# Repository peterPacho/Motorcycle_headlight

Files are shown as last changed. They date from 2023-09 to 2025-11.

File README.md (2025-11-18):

## Description
Riding at night is fun but I really didn't like the fact that I couldn't see where I'm going when turning.
This project aims to solve that issue by creating a headlight housing that can rotate, counteracting the motorcycle's lean during the turn, making the projected beam always parallel to the road surface.

Headlight bucket should fit most “Jeep” 7 inch headlights.

[V1 version demo video](https://www.youtube.com/watch?v=rBPONPm-cCk)

There are two MakerFocus TF-Luna lidars attached to the rear of the bike. Distance to the road surface is used to estimate the lean angle. I'm using Lidars since gyro/accelerometers proved to be difficult - I didn't find a way to counteract the centrifugal acceleration during the turn and couldn't obtain reliable data.

The "V3" version changes the overall design of the headlight housing. Migrating from multiple small bearing to two large ones, that would allow the wires to pass through the center, was done to reduce vibrations and friction. Those changes allowed headlight to be more responsive and reliable.

### Noncomprehensive parts list:
-	Arduino (and supporting components like resistors, voltage regulator, capacitors)
-	TMC2209 stepper motor driver
-	NEMA 17 stepper motor
-	16x2 LCD Display
-	80x100x10mm ball bearing x2

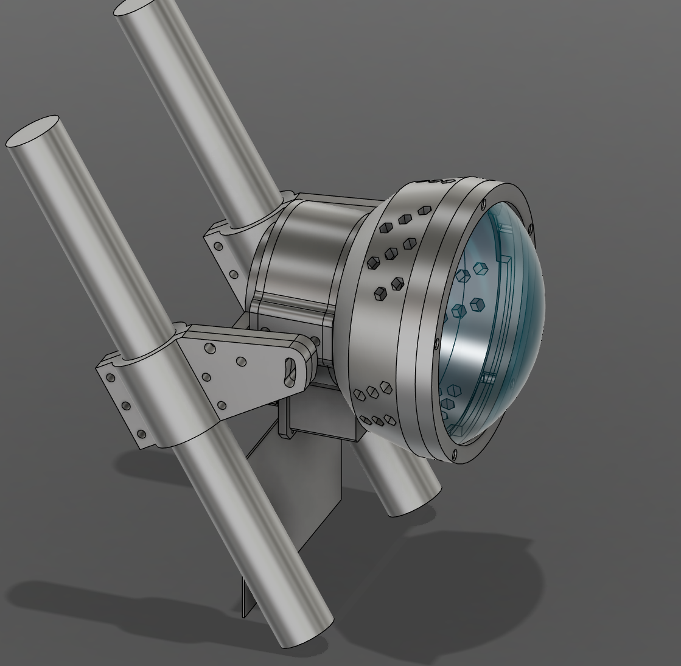
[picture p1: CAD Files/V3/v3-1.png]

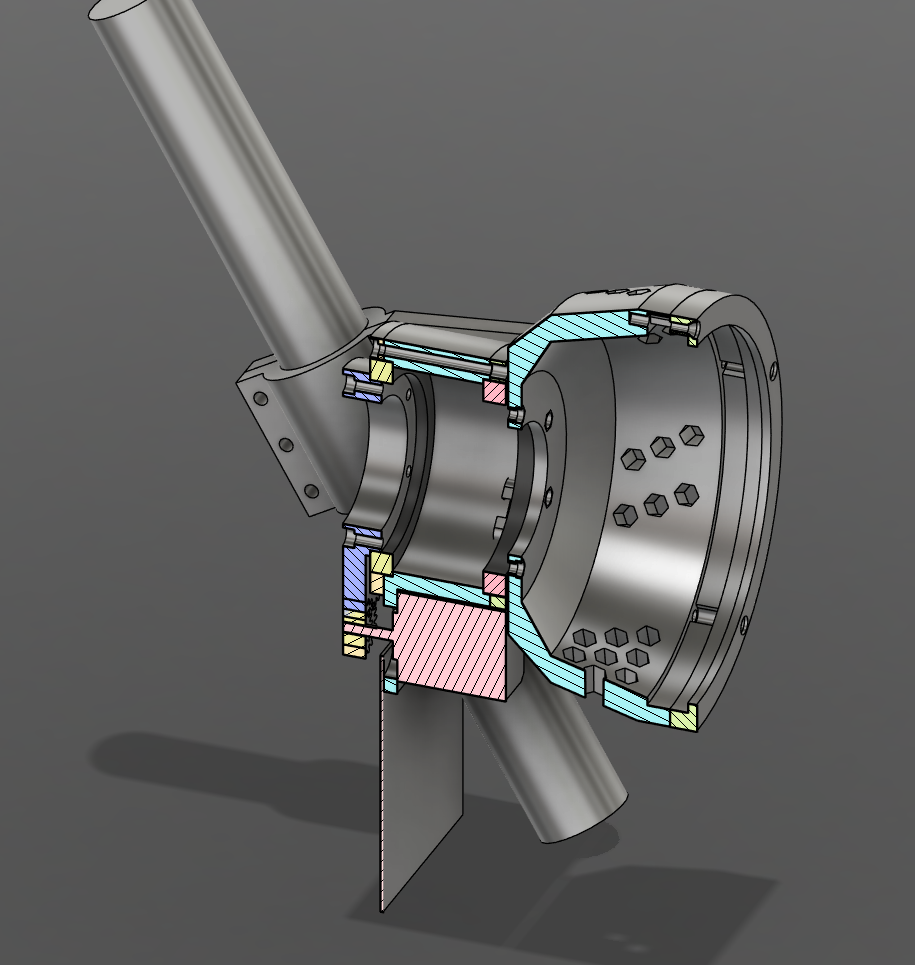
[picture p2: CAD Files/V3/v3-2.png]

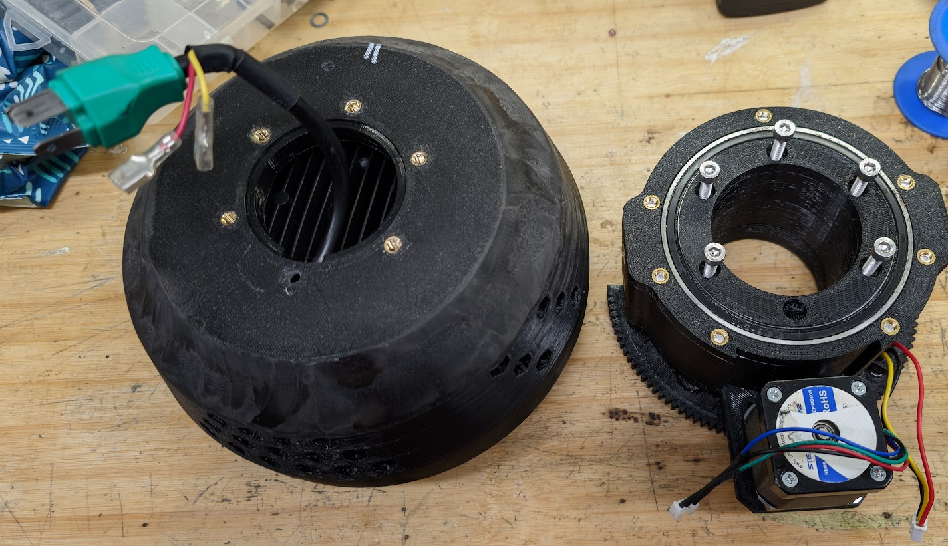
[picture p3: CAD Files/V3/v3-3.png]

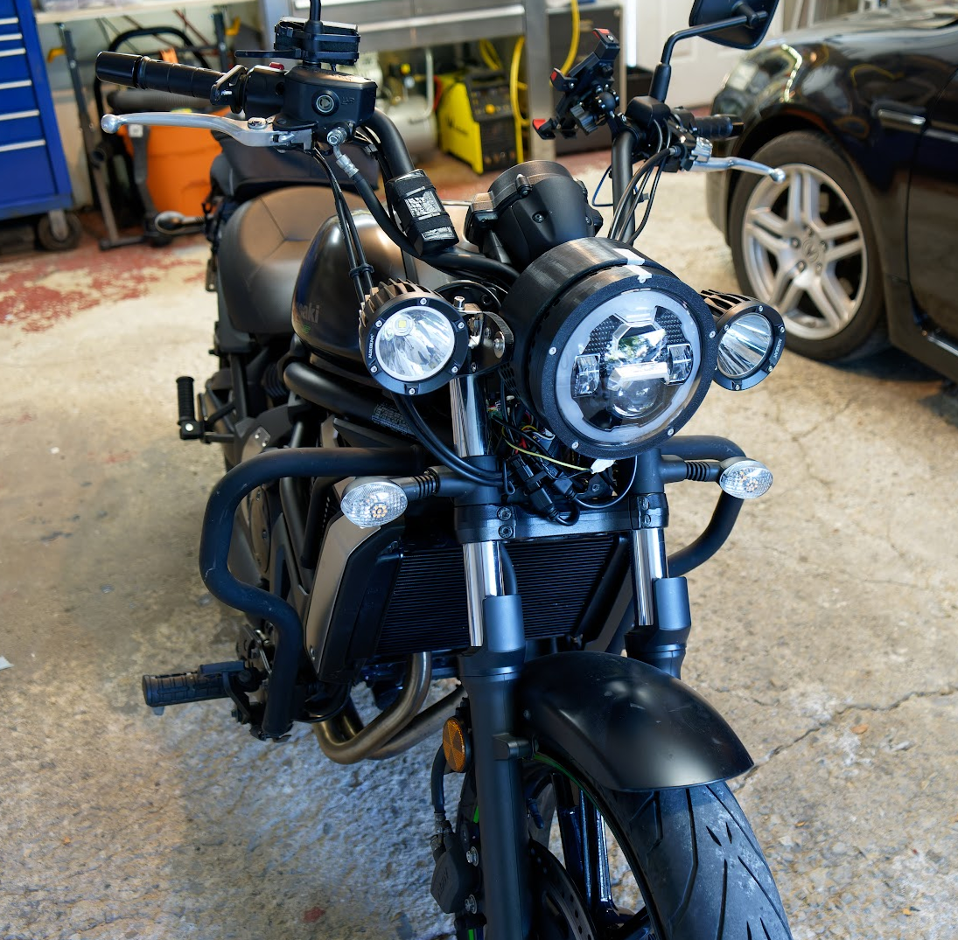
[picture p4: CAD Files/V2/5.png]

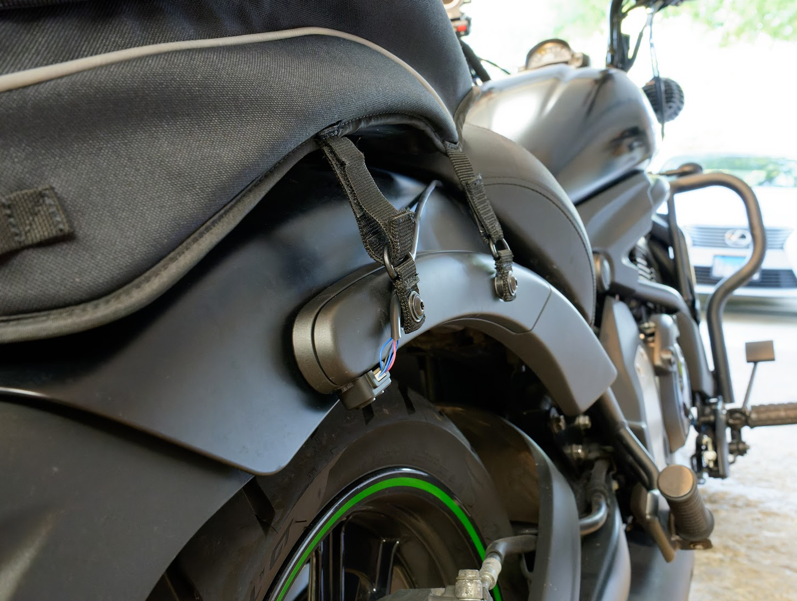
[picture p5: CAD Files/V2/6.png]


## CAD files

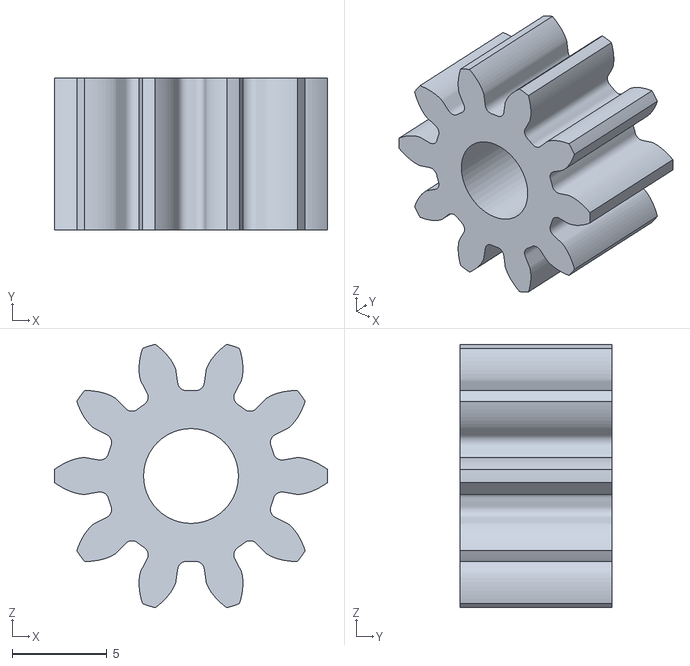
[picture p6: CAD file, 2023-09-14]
CAD Files/STL V2_3/Motorcycle Headlight version 2 v3_Motorcycle Headlight version 2 v3_Headlight outer bucket_1_Spur Gear (10 teeth) - Mod 1.2, Root fill 0.47 (1)_1_Body1.stl
14.4 x 8.00 x 13.9

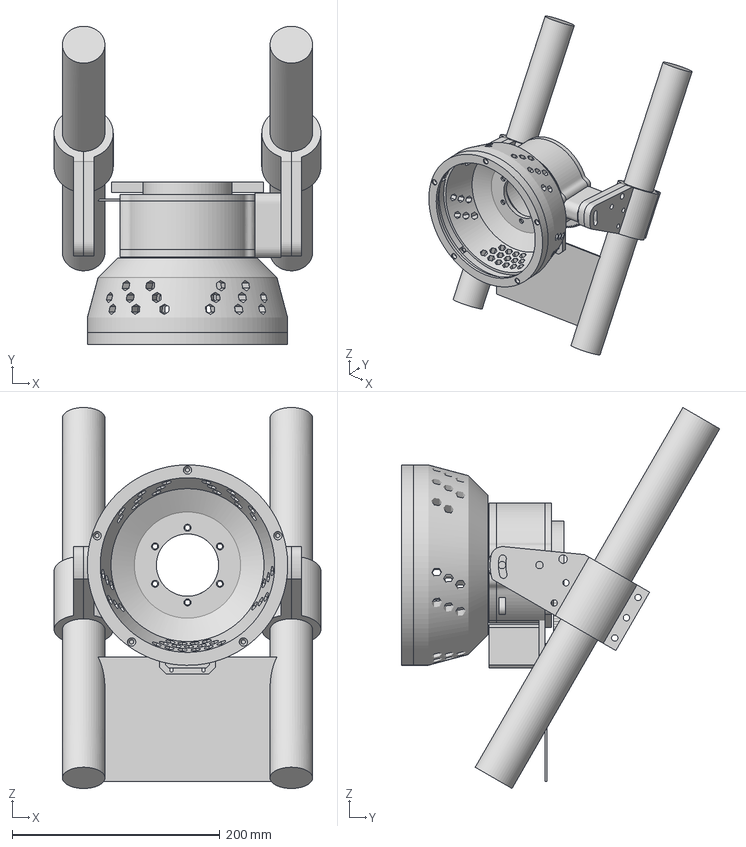
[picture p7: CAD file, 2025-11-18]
CAD Files/V3/Motorcycle Headlight V3-v22.3mf
257.0 x 306.6 x 366.9 mm
A x 2
B x 2
Back
Front-thread-inserts
Mid

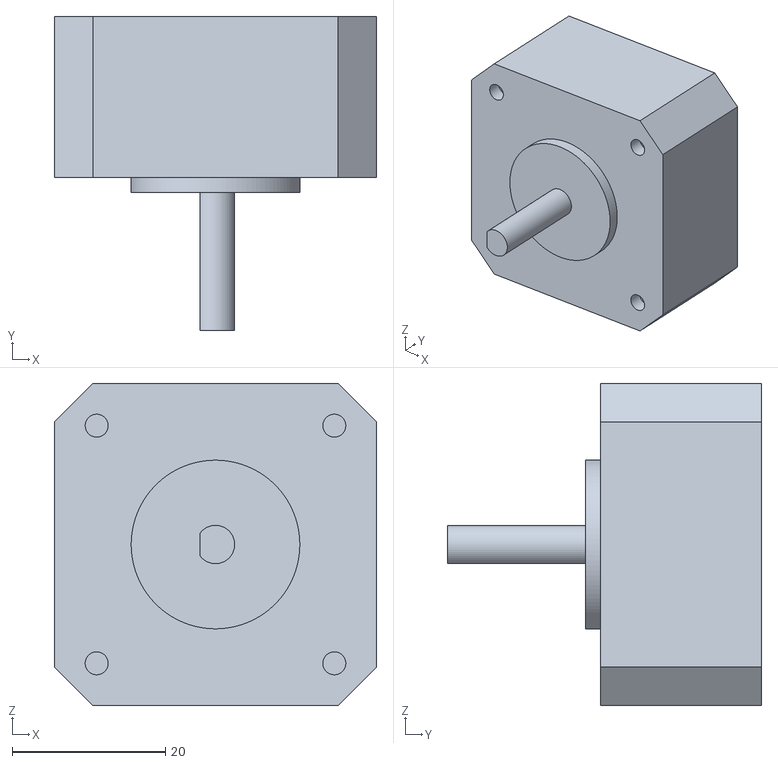
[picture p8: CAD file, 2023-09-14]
CAD Files/STL V2_3/Motorcycle Headlight version 2 v3_Motorcycle Headlight version 2 v3_Headlight outer bucket_1_Stepper_1_Body1.stl
42.0 x 41.0 x 42.0

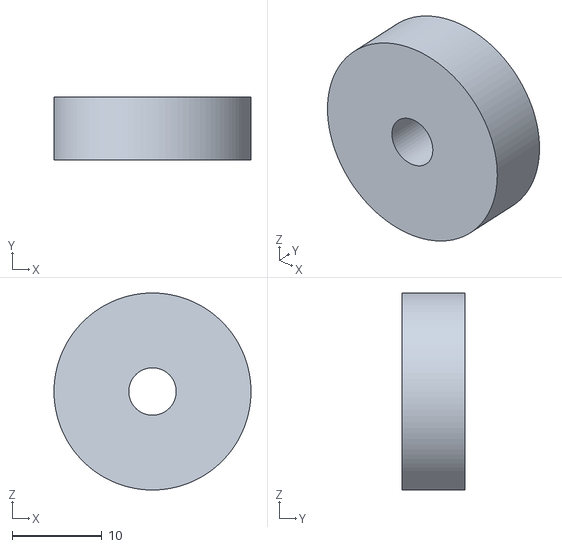
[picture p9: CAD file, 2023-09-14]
CAD Files/STL V2_3/Motorcycle Headlight version 2 v3_Motorcycle Headlight version 2 v3_Headlight inner bucket_1_Bearing_1_Body1.stl
22.0 x 7.00 x 22.0

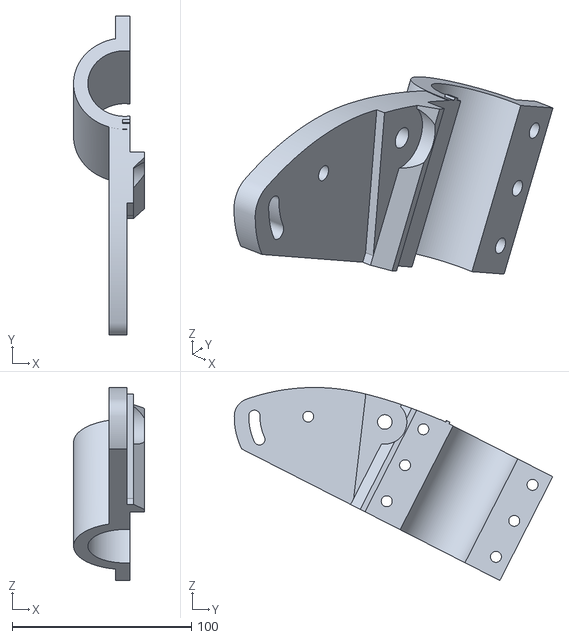
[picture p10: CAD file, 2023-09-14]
CAD Files/STL V2_3/Motorcycle Headlight version 2 v3_Motorcycle Headlight version 2 v3_Forks Mount V2(Mirror) (1)_1_Arm(Mirror) (1)_1_Body1.stl
39.5 x 177.5 x 107.6

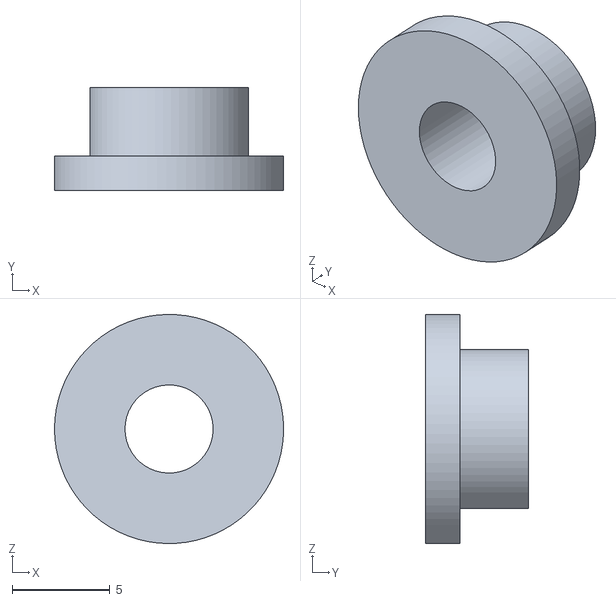
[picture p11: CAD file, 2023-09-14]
CAD Files/STL V2_3/Motorcycle Headlight version 2 v3_Motorcycle Headlight version 2 v3_Headlight inner bucket_1_Bearing sleeve_1_Body1.stl
11.7 x 5.25 x 11.7

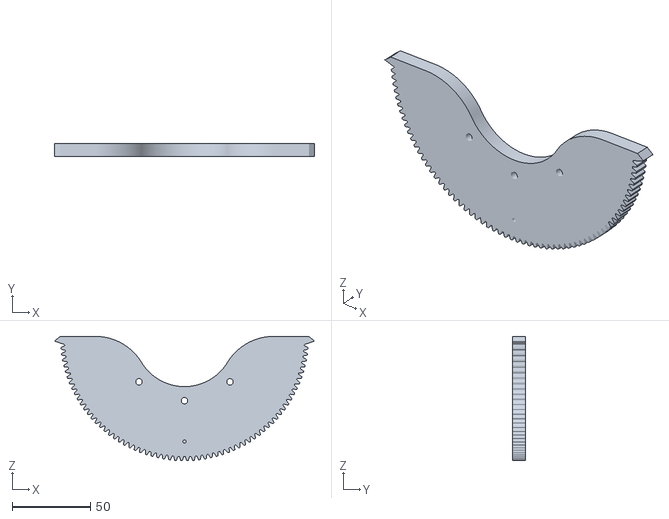
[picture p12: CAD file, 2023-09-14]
CAD Files/STL V2_3/Motorcycle Headlight version 2 v3_Motorcycle Headlight version 2 v3_Headlight inner bucket_1_Spur Gear (130 teeth) Mod 1.2, Root fill 0.47_1_Body1.stl
165.7 x 8.00 x 79.2

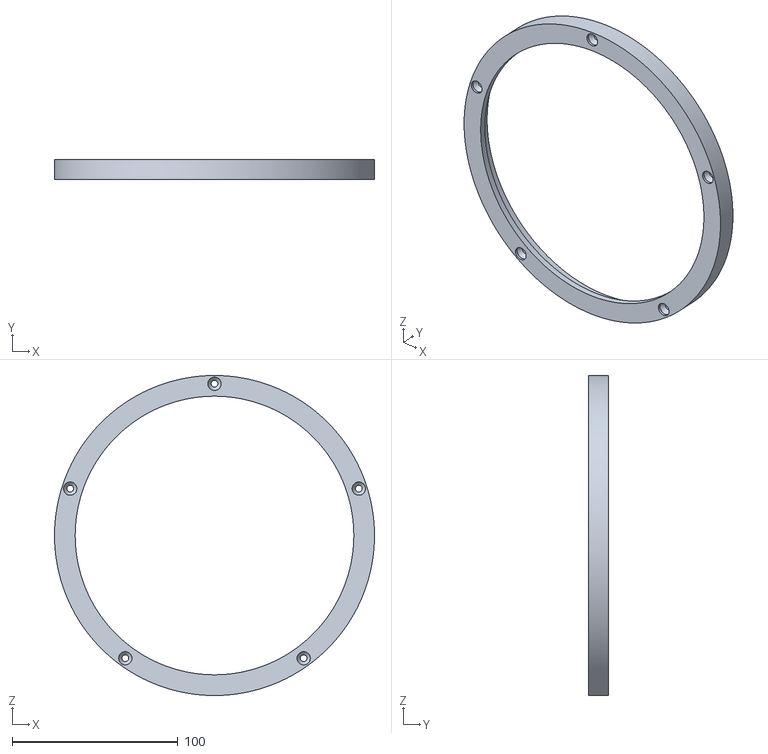
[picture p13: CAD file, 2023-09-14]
CAD Files/STL V2_3/Motorcycle Headlight version 2 v3_Motorcycle Headlight version 2 v3_Headlight inner bucket_1_Front_1_Body1.stl
193.0 x 12.0 x 193.0

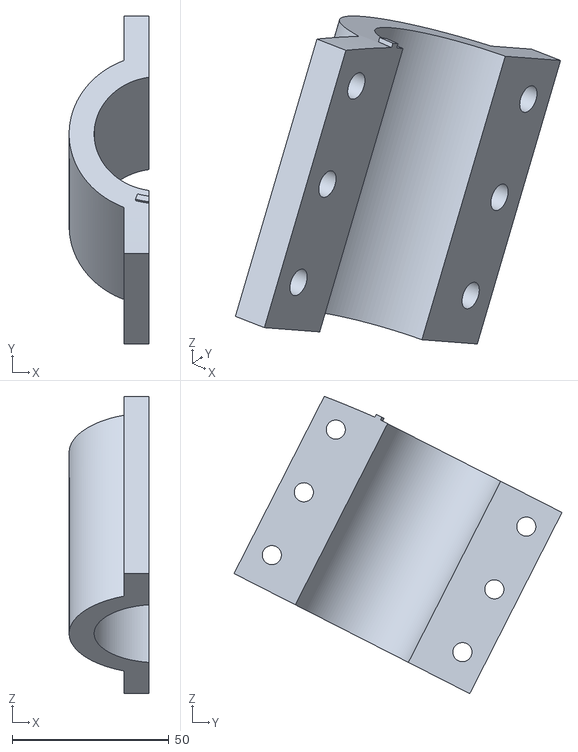
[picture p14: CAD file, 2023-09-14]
CAD Files/STL V2_3/Motorcycle Headlight version 2 v3_Motorcycle Headlight version 2 v3_Forks Mount V2_1_Clamp_1_Clamp.stl
25.5 x 104.8 x 95.0

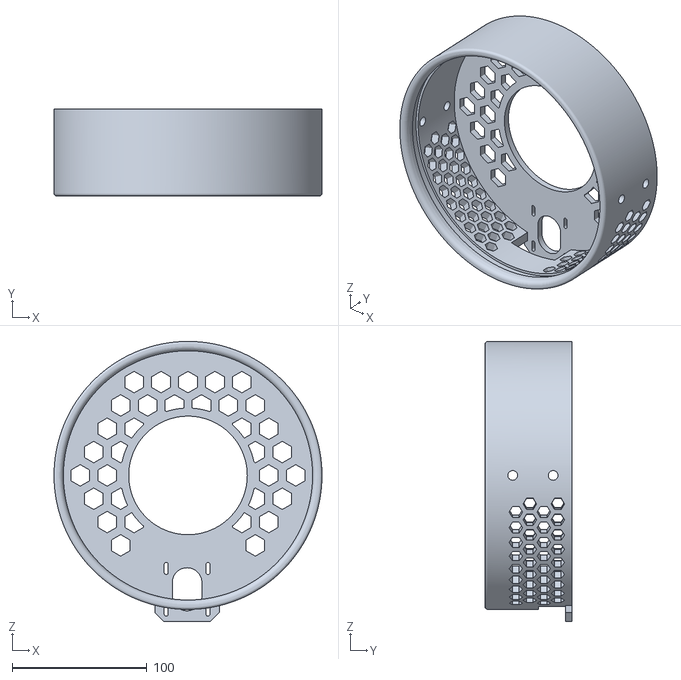
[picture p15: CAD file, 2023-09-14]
CAD Files/STL V2_3/Motorcycle Headlight version 2 v3_Motorcycle Headlight version 2 v3_Headlight outer bucket_1_Outer bucket_1_Body8.stl
199.0 x 64.6 x 208.0

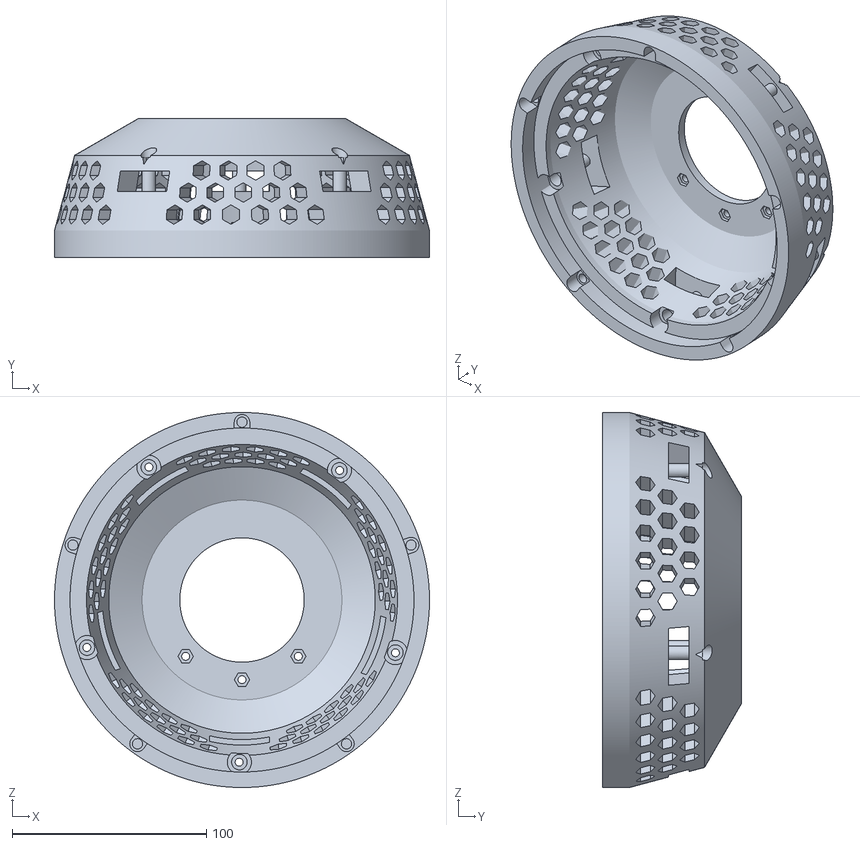
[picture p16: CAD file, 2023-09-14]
CAD Files/STL V2_3/Motorcycle Headlight version 2 v3_Motorcycle Headlight version 2 v3_Headlight inner bucket_1_Inner bucket nuts_1_Body1.stl
193.0 x 71.6 x 193.0

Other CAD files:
CAD Files/STL V2_3/Motorcycle Headlight version 2 v3_Motorcycle Headlight version 2 v3_Forks Mount V2_1_Arm_1_Body4.stl
CAD Files/STL V2_3/Motorcycle Headlight version 2 v3_Motorcycle Headlight version 2 v3_Headlight inner bucket_1_Bearing_1_Body6.stl
CAD Files/STL V2_3/Motorcycle Headlight version 2 v3_Motorcycle Headlight version 2 v3_Headlight inner bucket_1_Bearing_1_Body7.stl
CAD Files/STL V2_3/Motorcycle Headlight version 2 v3_Motorcycle Headlight version 2 v3_Headlight inner bucket_1_Bearing_1_Body9.stl
CAD Files/STL V2_3/Motorcycle Headlight version 2 v3_Motorcycle Headlight version 2 v3_Forks Mount V2(Mirror) (1)_1_Clamp(Mirror) (1)_1_Clamp.stl
CAD Files/STL V2_3/Motorcycle Headlight version 2 v3_Motorcycle Headlight version 2 v3_Headlight inner bucket_1_Bearing_1_Body8.stl
CAD Files/V2/Motorcycle Headlight version 2_v3.f3d

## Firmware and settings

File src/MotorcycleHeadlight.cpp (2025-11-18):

#include <Arduino.h>
#include <Wire.h>
#include <TMCStepper.h>	  // https://github.com/teemuatlut/TMCStepper
#include <AccelStepper.h> // https://github.com/teemuatlut/TMCStepper/blob/master/examples/TMC_AccelStepper/TMC_AccelStepper.ino
#include <LiquidCrystal_I2C.h>
#include <avr/eeprom.h>
#include <TFLI2C.h> // https://github.com/budryerson/TFLuna-I2C

// comment out to disable log/debug/serial commands and reduce sketch size
// #define DEBUG_ON

/*
	Comment out if uploading the sketch for the first time so
	it writes default settings to the Arduino's eeprom
*/
// #define RESTORE_DEFAULT_SETTINGS

/*
	Arduino pin-out. SDA (white wire) - A4, SCL (yellow/green wire) - A5
*/
const uint8_t
	DRIVER_ENABLE = 9,
	DRIVER_DIRECTION = 10,
	DRIVER_STEP = 13,
	DRIVER_SWCLCK = 11,
	DRIVER_TX = 6,
	DRIVER_RX = 12,

	HALL_SENSOR = 4, // sensor that detects the center position of the headlight
	BUTTON1 = 7,
	BUTTON2 = 8,
	BUTTON3 = A1,
	BUTTON4 = A2,
	LCD_BRIGHTNESS = 3,	   // must be a PWM pin, used to set custom LCD brightness that extends the build-in on/off
	VOLTAGE_SENSE = A0,	   // connected to voltage divider and 12V input
	LUNA_ENABLE_RELAY = 2; // pin that disables one of Luna modules so the address of the other one can be changed

#define DRIVER_ADDRESS 0b00
#define DRIVER_RSENSE 0.11f
#define MPU 0x68
#define LUNA_ADDRESS_1 0x10 // this must be the default luna address
#define LUNA_ADDRESS_2 0x11 // luna that is not connected through relay will have address changed to this value

/*
	With 72:8 gear ratio (9:1),
	stepper motor having 1.8 degrees per step
	and microsteps set to 16
	it takes 360 * 9 * 16 / 1.8 = 28800 steps for full rev.

	With 130:10 / 13:1 gear ratio and 2 micro steps = 5200
	With 120:12 and 2 micro steps = 4800
	With 120:20 and 2 micro steps = 2400
*/
#define DRIVER_MICROSTEPS 2					  // to disable microsteps change this to 0
#define STEPS_PER_REVOLUTION 2400			  // used by the centering function
#define STEPS_LIMIT STEPS_PER_REVOLUTION * .2 // How many steps it takes to reach end of travel from the center. Limits the headlight's maximum angle.

SoftwareSerial SoftSerial(DRIVER_RX, DRIVER_TX);
TMC2209Stepper TMCdriver(&SoftSerial, DRIVER_RSENSE, DRIVER_ADDRESS);
AccelStepper stepper = AccelStepper(stepper.DRIVER, DRIVER_STEP, DRIVER_DIRECTION);
LiquidCrystal_I2C lcd(0x27, 16, 2);
TFLI2C tflI2C;

/*
	The idea to store/save settings like this it taken from
	catalkn's post at https://forum.arduino.cc/t/how-to-save-configuration/45314/6
*/
struct SETTINGS_S
{
	int DRIVER_MAX_SPEED = STEPS_PER_REVOLUTION / 4; // in steps per second, with 2A and 120:20 gear ratio, this should be ~500
	int DRIVER_MAX_ACC = STEPS_PER_REVOLUTION / 4;	 // in steps per second, with 2A and 120:20 gear ratio, this should be ~1500
	int DRIVER_CURRENT = 1000;						 // in mA?, bigger nema should be fine at 2A
	int DISPLAY_BRIGHTNESS = 100;					 // 0-255
	int SENSOR_UPDATE_TIME = 25;					 // in ms, how often to read data from the lunas
	int STEPS_LIMIT_ALLOWED = STEPS_LIMIT;			 // STEPS_LIMIT sets how many steps are allowed by hardware (physical stop), this limits it further
	int MOVE_THRESHOLD = 2;							 // how many steps off "correct" position before is starts moving
	int MOVE_THRESHOLD_CENTER = 5;					 // how many steps off center before it starts moving
	int SPEED_THRESHOLD = 200;						 // if current speed above this # of steps, don't read lunas to prevent skipping the steps
	char STARTUP_MODE = -1;							 // what should be the mode after first start, -1 default, 0 or 1 will call calibration function
	float VOLTAGE_WEIGHTING_PARAMETER = 0.1;		 // to filter voltage readings
	float SENSOR_WEIGHTING_PARAMETER = 0.1;			 // to filter LUNA readings
} const DEFAULT_SETTINGS;

SETTINGS_S SETTINGS = DEFAULT_SETTINGS;
// void eeprom_update_block(const void*, void*, size_t); //defined so VS code doesn't complain
// void eeprom_read_block(void*, const void*, size_t);

void loadSettings()
{
	eeprom_read_block((void *)&SETTINGS, (void *)0, sizeof(SETTINGS));

	TMCdriver.rms_current(SETTINGS.DRIVER_CURRENT);
	stepper.setMaxSpeed(SETTINGS.DRIVER_MAX_SPEED);
	stepper.setAcceleration(SETTINGS.DRIVER_MAX_ACC);
	analogWrite(LCD_BRIGHTNESS, SETTINGS.DISPLAY_BRIGHTNESS);
}

void saveSettings()
{
	eeprom_update_block((const void *)&SETTINGS, (void *)0, sizeof(SETTINGS));
}

/*
	If uploading the sketch first time call this function!
	Don't enable the stepper driver or bad things might happen.
*/
void restoreDefaultSettings()
{
	SETTINGS = DEFAULT_SETTINGS;
	TMCdriver.rms_current(SETTINGS.DRIVER_CURRENT);
	stepper.setMaxSpeed(SETTINGS.DRIVER_MAX_SPEED);
	stepper.setAcceleration(SETTINGS.DRIVER_MAX_ACC);
	analogWrite(LCD_BRIGHTNESS, SETTINGS.DISPLAY_BRIGHTNESS);

	saveSettings();
}

char mode = -1; // used in main loop to turn on/off gyro function

// debouncing class for simple buttons, default for them is high (internal pull up)
unsigned long lastButtonEvent = 0; // keeps time when was the button pressed last time
class button
{
public:
	// constructor that sets all variables to default
	button(byte buttonID_c)
	{
		pinMode(buttonID_c, INPUT_PULLUP);

		// update all variables
		buttonID = buttonID_c;
		buttonDebounce = 0;
		buttonLastState = HIGH;
		buttonCurrentState = HIGH;
		buttonPressUsed = true;
	}

	// returns 1 if pressed, returns 2 if being hold
	int state()
	{
		// read actual button state
		buttonCurrentState = digitalRead(buttonID);

		// check if it changed from last time, if it did take note of the time
		if (buttonCurrentState != buttonLastState)
			buttonDebounce = millis();

		// update the last state variable
		buttonLastState = buttonCurrentState;

		// check if button is being held down
		if (millis() - buttonDebounce > buttonHoldTimer && buttonCurrentState == LOW)
		{
			lastButtonEvent = millis();

			// prevent from setting the "isPressed" and "isHeld" signal simultaneously
			buttonPressUsed = true;

			return 2;
		}

		// now check if button is in its current state for long enough, but trigger only if button is let go
		else if ((millis() - buttonDebounce) > buttonDebounceDelay && millis() - buttonDebounce < buttonHoldTimer)
		{
			// remember to return true only once per button press
			// to prevent value increase when button is being hold
			if (!buttonPressUsed && buttonCurrentState == HIGH)
			{
				buttonPressUsed = true;

				// if so, update the optional variable, if set
				lastButtonEvent = millis();

				return 1;
			}

			// if not pressed, reset the 'use' variable
			if (buttonCurrentState == LOW)
				buttonPressUsed = false;
		}

		return 0;
	}

private:
	byte buttonID;								  // holds button id, like A1
	unsigned long buttonDebounce;				  // holds time when button changed last time
	int buttonLastState;						  // what was last button state
	int buttonCurrentState;						  // what is current state
	bool buttonPressUsed;						  // if button was determined to be pressed, use this to return true only once
	const unsigned long buttonDebounceDelay = 20; // minimum delay between change of signals
	const unsigned long buttonHoldTimer = 400;	  // how long to hold the button before it's considered being hold
};
button buttonOK(BUTTON4);
button buttonUp(BUTTON3);
button buttonDown(BUTTON1);
button buttonESC(BUTTON2);

/*
	Finds the center / calibrates the stepper using the hall sensor.
*/
void calibratePosition()
{
	// setup
	int direction = 1;

	lcd.clear();
	lcd.setCursor(0, 0);
	lcd.print(F("Calibrating"));
	lcd.setCursor(4, 1);
	lcd.print(F("position..."));
	if (digitalRead(DRIVER_ENABLE))
	{
		stepper.enableOutputs();
		delay(300);
	}
	stepper.setMaxSpeed(SETTINGS.DRIVER_MAX_SPEED / 3);
	stepper.setAcceleration(SETTINGS.DRIVER_MAX_ACC / 3);

	// if already calibrated before, move to 0 to reduce time
	// if just started or already on 0 this function returns 0
	if (stepper.currentPosition())
	{
		stepper.moveTo(0);
		while (stepper.distanceToGo())
			stepper.run();
		// if moved to 0 but still didn't reach HALL (due to some missed steps??) go a bit further
		if (digitalRead(HALL_SENSOR))
			stepper.moveTo(STEPS_PER_REVOLUTION * 0.04);
		while (stepper.distanceToGo())
			stepper.run();
	}

	// arbitrary multiplier - want to move not more than less than 45 degrees
	stepper.move(-STEPS_PER_REVOLUTION * 0.25);

	while (stepper.distanceToGo() != 0 && digitalRead(HALL_SENSOR))
	{
		stepper.run();
	}

	stepper.setCurrentPosition(0);

	//	if hall still reads high, we must be past it (and stalled on the end stop), so rotate back to the middle
	if (digitalRead(HALL_SENSOR))
	{
		direction = direction * -1; // set so next steps of finding the center accelerate in the same direction

		stepper.move(STEPS_PER_REVOLUTION * 0.3);

		while (stepper.distanceToGo() != 0 && digitalRead(HALL_SENSOR))
		{
			stepper.run();
		}
	}

	stepper.setCurrentPosition(0);

	// at this point we more or less should be in the middle
	// hall should read 0
	// so do small steps to actually find the middle
	stepper.setMaxSpeed(SETTINGS.DRIVER_MAX_SPEED / 6);
	stepper.setAcceleration(SETTINGS.DRIVER_MAX_ACC / 6);

	// again arbitrary multiplier - too small and we don't reach other side of the magnet
	stepper.move(-STEPS_PER_REVOLUTION * 0.04 * direction);

	while (stepper.distanceToGo() != 0 && !digitalRead(HALL_SENSOR))
	{
		stepper.run();
	}

	// reached some point where hall no longer reads 0
	// reset position to 0
	// move in other direction until hall reads 0 and then reads 1 again

	stepper.setCurrentPosition(0);
	stepper.move(STEPS_PER_REVOLUTION * 0.04 * direction);

	while (stepper.distanceToGo() != 0 && digitalRead(HALL_SENSOR))
	{
		stepper.run();
	}
	while (stepper.distanceToGo() != 0 && !digitalRead(HALL_SENSOR))
	{
		stepper.run();
	}

	// go back to the previous settings
	stepper.setMaxSpeed(SETTINGS.DRIVER_MAX_SPEED);
	stepper.setAcceleration(SETTINGS.DRIVER_MAX_ACC);

	// now reached other side of the hall range, so actual middle position is somewhere in between
	stepper.moveTo(stepper.currentPosition() / 2);

	while (stepper.distanceToGo() != 0)
		stepper.run();

	// now we are in the actual middle position
	stepper.setCurrentPosition(0);

	lcd.clear();
}

#ifdef DEBUG_ON
/*
	Taken from https://learn.adafruit.com/scanning-i2c-addresses/arduino
*/
void findDevices()
{
	byte error, address;
	int nDevices;

	Serial.println(F("Scanning..."));

	nDevices = 0;
	for (address = 1; address < 127; address++)
	{
		// The i2c_scanner uses the return value of
		// the Write.endTransmission to see if
		// a device did acknowledge to the address.
		Wire.beginTransmission(address);
		error = Wire.endTransmission();

		if (error == 0)
		{
			Serial.print(F("I2C device found at address 0x"));
			if (address < 16)
				Serial.print(F("0"));
			Serial.println(address, HEX);

			nDevices++;
		}
		else if (error == 4)
		{
			Serial.print(F("Unknown error at address 0x"));
			if (address < 16)
				Serial.print(F("0"));
			Serial.println(address, HEX);
		}
	}
	if (nDevices == 0)
		Serial.println(F("No I2C devices found\n"));
	else
		Serial.println(F("done\n"));
}

/*
	Processes the serial commands for debugging
*/
void serialCommands()
{
	if (Serial.available())
	{
		String data = Serial.readString();

		switch (data.charAt(0))
		{
		case 's':
		{
			int speed = data.substring(1).toInt();

			if (speed == 0)
			{
				stepper.disableOutputs();
				Serial.println(F("Stepper disabled"));
			}
			else
			{
				Serial.print(F("Speed set to "));
				Serial.println(speed);
				stepper.enableOutputs();
				stepper.setMaxSpeed(speed);
			}
			break;
		}

		case 'p':
		{
			int position = data.substring(1).toInt();
			Serial.print(F("Moving stepper to position "));
			Serial.println(position);
			stepper.moveTo(position);
			break;
		}

		case 'a':
		{
			int speed = data.substring(1).toInt();

			Serial.print(F("Acceleration set to "));
			Serial.println(speed);
			stepper.enableOutputs();
			stepper.setAcceleration(speed);
			break;
		}

		case 'c':
		{
			calibratePosition();
			break;
		}
		case 'd':
		{
			Serial.println(F("Stepper disabled."));
			stepper.disableOutputs();
			break;
		}
		default:
			Serial.println(F("Unknown command!"));
		}
	}
}

#endif

/*
	Those values were obtained by gathering data on different voltage levels and doing
	the linear curve fit in LoggerPro. More accurate than calculating from resistor's values used and requires less brain power.
*/
float voltMeter()
{
	// static byte voltageHistoryCounter = 0;
	// static int voltageHistory[VOLTAGE_HISTORY_SIZE] = {0};

	// voltageHistory[voltageHistoryCounter] = analogRead(VOLTAGE_SENSE);
	// voltageHistoryCounter++;
	// if (voltageHistoryCounter >= VOLTAGE_HISTORY_SIZE)
	// 	voltageHistoryCounter = 0;

	// unsigned long historySum = 0;
	// for (int i = 0; i < VOLTAGE_HISTORY_SIZE; i++)
	// {
	// 	historySum += voltageHistory[i];
	// }
	static float previousValue = 0;
	float currentValue = (float)analogRead(VOLTAGE_SENSE) * 0.02764 + 0.0708;
	previousValue = previousValue * (1 - SETTINGS.VOLTAGE_WEIGHTING_PARAMETER) + currentValue * SETTINGS.VOLTAGE_WEIGHTING_PARAMETER;

	return currentValue;
}

void setup()
{
#ifdef RESTORE_DEFAULT_SETTINGS
	restoreDefaultSettings();
#endif

	eeprom_read_block((void *)&SETTINGS, (void *)0, sizeof(SETTINGS));

#ifdef DEBUG_ON
	Serial.begin(115200);
	Serial.print(F("Setup begin...  "));
#endif
	SoftSerial.begin(9600);
	TMCdriver.beginSerial(9600);

	Wire.begin();

	lcd.init();
	lcd.noBacklight(); // as brightness is controlled by arduino, LCD is modified to allow that
	analogWrite(LCD_BRIGHTNESS, SETTINGS.DISPLAY_BRIGHTNESS);
	lcd.clear();
	lcd.setCursor(0, 0);
	lcd.print(F("Starting..."));

	digitalWrite(DRIVER_ENABLE, HIGH);
	pinMode(DRIVER_ENABLE, OUTPUT);
	pinMode(DRIVER_DIRECTION, OUTPUT);
	pinMode(DRIVER_STEP, OUTPUT);
	pinMode(HALL_SENSOR, INPUT_PULLUP);
	pinMode(VOLTAGE_SENSE, INPUT);

	/*
		disable one of the luna sensors to change other luna's address
		luna power connected to normally closed relay, so writing 1 opens the relay
	*/
	pinMode(LUNA_ENABLE_RELAY, OUTPUT);
	digitalWrite(LUNA_ENABLE_RELAY, 1);

	TMCdriver.begin();
	TMCdriver.rms_current(SETTINGS.DRIVER_CURRENT);
	TMCdriver.pwm_autoscale(1);
	TMCdriver.microsteps(DRIVER_MICROSTEPS);

	stepper.setMaxSpeed(SETTINGS.DRIVER_MAX_SPEED);
	stepper.setAcceleration(SETTINGS.DRIVER_MAX_ACC);
	stepper.setEnablePin(DRIVER_ENABLE);
	stepper.setPinsInverted(false, false, true);
	stepper.disableOutputs();

	if (SETTINGS.STARTUP_MODE != -1)
	{
		calibratePosition();
		mode = SETTINGS.STARTUP_MODE;
	}

	// if luna found on the default address, change it
	// if arduino rebooted without power cycling luna, it won't respond to this address
	Wire.beginTransmission(LUNA_ADDRESS_1);
	if (Wire.endTransmission() == 0)
	{
		tflI2C.Set_I2C_Addr(LUNA_ADDRESS_2, LUNA_ADDRESS_1);
	}
	digitalWrite(LUNA_ENABLE_RELAY, 0); // enable the second luna

#ifdef DEBUG_ON
	Serial.println(F(" done."));
#endif
}

/*
	Used to set numerical setting values.

	Input:
		- startValue - current setting/value
		- min, max - allowed range for that setting
		- multiplier - how much value should change per single button event

	Returns:
		- if ESC button pressed - original/unchanged startValue
		- if OK pressed - currently set/displayed value
*/
int menuInner(int startValue, int min, int max, int y, int multiplier = 1)
{
	int setValue = startValue;
	int displayedValue = startValue + 1; // to make sure display updates this time

	// figure out maximum number of characters needed to display the value
	int maxLength = String(max).length();
	int maxLength2 = String(min).length() + 1;
	if (maxLength2 > maxLength)
		maxLength = maxLength2;

	while (1)
	{
		if (displayedValue != setValue)
		{
			// clear the fields
			for (int i = 16 - maxLength; i <= 15; i++)
			{
				lcd.setCursor(i, y);
				lcd.print(F(" "));
			}

			// figure out how many characters we need
			lcd.setCursor(16 - String(setValue).length(), y);

			lcd.print(setValue);

			displayedValue = setValue;
		}

		if (buttonUp.state())
		{
			setValue += multiplier;
			if (setValue > max)
				setValue = max;
		}
		else if (buttonDown.state())
		{
			setValue -= multiplier;
			if (setValue < min)
				setValue = min;
		}
		else if (buttonESC.state())
		{
			return startValue;
		}
		else if (buttonOK.state() == 1)
		{
			return setValue;
		}
	}
}
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
void loop()
{
#ifdef DEBUG_ON
	serialCommands();
	static unsigned long lastLogEvent = 0;
	if (millis() - lastLogEvent > 500)
	{
		Serial.println(stepper.speed());

		lastLogEvent = millis();
	}

#endif

	static float bikeLeanAngle = 0;
	static int previousTarget = 0; // what was the target stepper position
	int16_t lunaDist1 = 0, lunaDist2 = 0;
	bool lunaReadingResult = false;

	/*

	*/
	do
	{
		stepper.run();
	} while (abs(stepper.speed()) > SETTINGS.SPEED_THRESHOLD);
	/*
		Todo:
		- this "300" value, make it a setting
		- migrate settings menu from 5160 branch
	*/

	/*
		Update the sensors.
		Reading one sensor at the time.
	*/
	static unsigned long lastSensorUpdate = 0;
	bool updateLunas = millis() - lastSensorUpdate > (unsigned long)SETTINGS.SENSOR_UPDATE_TIME;
	if (updateLunas)
	{
		lunaReadingResult = tflI2C.getData(lunaDist1, LUNA_ADDRESS_1);
	}

	stepper.run();

	/*
		Reading second luna
	*/
	// unsigned long start = micros(), end;
	if (updateLunas)
	{
		lunaReadingResult = lunaReadingResult && tflI2C.getData(lunaDist2, LUNA_ADDRESS_2);

		if (lunaReadingResult)
		{
			bikeLeanAngle = getBikeAngle(lunaDist1 - lunaDist2);

			lastSensorUpdate = millis();
		}
	}

	/*
		Stepper motor control.
	*/
	if (mode == 1)
	{
		// bikeLeanAngle is in degrees off center
		int newTarget = bikeLeanAngle * STEPS_PER_REVOLUTION / 4 / 90;

		if (abs(newTarget) < SETTINGS.MOVE_THRESHOLD_CENTER)
		{
			newTarget = 0;
			previousTarget = 0;
			stepper.moveTo(0);
		}
		else if (abs(newTarget - previousTarget) > SETTINGS.MOVE_THRESHOLD)
		{
			if (newTarget > SETTINGS.STEPS_LIMIT_ALLOWED)
				newTarget = SETTINGS.STEPS_LIMIT_ALLOWED;
			else if (newTarget < -SETTINGS.STEPS_LIMIT_ALLOWED)
				newTarget = -SETTINGS.STEPS_LIMIT_ALLOWED;

			stepper.moveTo(newTarget);

			previousTarget = newTarget;
		}
	}
	// end = micros();
	// end = end - start;
	// if (end > 100)
	// 	Serial.println(end);

	// if stepper not in target position don't run rest of the function.
	// less important parts after this step
	if (stepper.distanceToGo())
	{
		return;
	}

	/*
		Check for user input.
		Only very important button checks here as it's possibly
		done when stepper driver is running.
	*/
	switch (buttonOK.state())
	{
	case 1:
		if (mode == -1)
		{
			calibratePosition();
			mode = 0;
		}
		else
		{
			if (mode == 0)
				mode = 1;
			else
				mode = 0;

			if (!mode)
			{
				stepper.moveTo(0);
				previousTarget = 0;
			}
		}
		break;

		// if button is held down, recalibrate without changing the mode
	case 2:
		int modeSave = mode;

		calibratePosition();

		if (modeSave == 1)
			mode = 1;
		else
			mode = 0;

		break;
	}

	if (buttonESC.state())
	{
		// if we were calibrated and possibly running, go back to the center before entering the menu
		if (mode != -1)
			stepper.moveTo(0);
		while (stepper.distanceToGo())
			stepper.run();

		stepper.disableOutputs();
		mode = -1;
		menu_main();
		return;
	}
	else if (buttonDown.state() == 2)
	{
		mode = -1;
		stepper.disableOutputs();
	}

	/*
		Update the display.
	*/
	static unsigned long lastDisplayUpdate = 0;
	if (millis() - lastDisplayUpdate > 300)
	{
		lcd.clear();
		lcd.setCursor(0, 0);

		lcd.print(F("Status:"));
		lcd.setCursor(0, 1);
		if (mode == 0)
			lcd.print(F("OFF"));
		else if (mode == 1)
			lcd.print(F("ON"));
		else if (mode == -1)
		{
			static byte msg_counter = 0;

			if (msg_counter < 3)
				lcd.print(F("press OK"));
			else if (msg_counter < 6)
				lcd.print(F("to"));
			else
				lcd.print(F("calibrate"));

			msg_counter++;
			if (msg_counter > 9)
				msg_counter = 0;
		}
		else
			lcd.print(F("err"));

		float volts = voltMeter();
		if (volts >= 10)
			lcd.setCursor(10, 1);
		else
			lcd.setCursor(11, 1);
		lcd.print(volts);
		lcd.print(F("V"));

		int printOffset = 0;
		if (bikeLeanAngle < 0)
			printOffset--;
		if (abs(bikeLeanAngle) >= 10)
			printOffset--;
		if (abs(bikeLeanAngle) >= 100)
			printOffset--;

		lcd.setCursor(printOffset + 12, 0);
		lcd.print(bikeLeanAngle);

		lastDisplayUpdate = millis();
	}
}

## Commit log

2023-07-30 Migrating to different gyro board
2023-08-03 migrated to BNO055 gyro
2023-08-12 menu and sensor calibration
2023-08-16 migrated to WT901 gyroscope
2023-08-19 removed the gyro from the sketch
2023-08-19 Delete JY901.zip
    No longer using this gyro
2023-09-02 moved to luna sensor test1
2023-09-14 added CAD files
    [Motorcycle Headlight version 2 v3_Motorcycle Headlight version 2 v3_Forks Mount V2(Mirror) (1)_1_Arm(Mirror) (1)_1_Body1.stl, Motorcycle Headlight version 2 v3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]
2024-06-22 Moved to Platformio, some code changes
    Moved the Arduino project to use Platformio. Also changed the gear ratio and added test menu.
2025-11-18 added v3 files
    [Motorcycle Headlight V3-v22.3mf, Motorcycle Headlight version 2_v3.f3d]
